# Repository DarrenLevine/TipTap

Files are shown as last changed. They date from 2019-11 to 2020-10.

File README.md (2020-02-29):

# TipTap

A 3d-printed bipedal robot. A low-cost desktop option for semi-direct drive walking research.

AssembledRobotAnimation

## Software

### Dependencies

* python >= 3.5
* pybullet
* numpy

A single python library "tiptap.py" is provided to interface to both Simulation and Hardware.
Its provides identical function calls on either target, so that you can develop your control
algorithms in simulation, and then run the idential script on hardware
without any extra work to port your code from simulation to hardware.

To get started, run, and read:
**software/example_OperatingTipTap.py**

If you're not connected to hardware a pybullet simulation will automatically start:
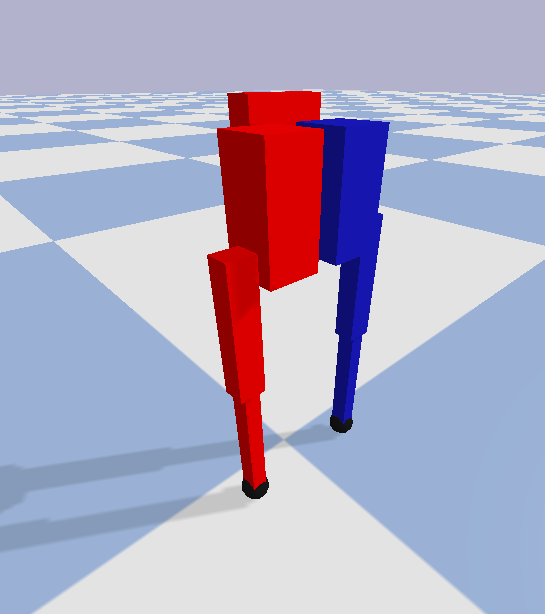
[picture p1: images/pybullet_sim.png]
pybullet_sim


If you are connected to hardware, you'll automatically be able to control the robot.

## Components

Please let me know if you find these directions difficult or find mistakes, thank you!

### Manufactured Components

* Qty 4. TipTap Motors: <https://github.com/DarrenLevine/TipTapMotor>

### Printed Components

Note: I used the parts/LulzbotMini_TipTap.curaprofile on my lulzbot mini to print all of the parts in esun PLA+.

* Qty 1. parts/BeagleBoneBlue_CaseW_RS485USB-Inner.STL
* Qty 1. parts/BeagleBoneBlue_CaseW_RS485USB-Outer.STL
* Qty 2. parts/DualMotorPCBspacer.STL
* Qty 2. parts/HipPulleyHub-Gear.STL
* Qty 2. parts/HipPulleyHub-PressurePlate.STL
* Qty 4. parts/LowerLeg.STL
* Qty 1. parts/PelvisBracket.STL
* Qty 1. parts/PelvisBracketForServos_WBuckConv.STL
* Qty 2. parts/SwivelPlate.STL
* Qty 2. parts/SwivelPlateMirror.STL
* Qty 2. parts/SwivelPlateServoMount.STL
* Qty 2. parts/SwivelPlateServoMountMirror.STL
* Qty 2. parts/UpperLegGeared-Leg.STL
* Qty 2. parts/UpperLegGeared-PressurePlate.STL
* Qty 2. parts/UpperLegHubGear.STL
* Qty 2. parts/UpperLegOuter.STL

### Purchased Components

* Qty 4. 623ZZ 3mm x 10mm x 4mm Shielded Deep Groove Precision Ball Bearing
* Qty 6. MR63ZZ L-630 673ZZ Ball Bearings
* Qty 2. AST 6706-2RS Thin Section Bearing
* Qty 2. MG92B servos
* Qty 2. BESTORQ 300-3M-6 3M Timing Belt
* Qty 1. BeagleBone Blue (BBB)
* Qty 1. LM2596 Buck Converter (set to output ~7.4v for the BBB)
* Qty 1. Mini Micro ZH 1.5 3-Pin JST Connector (to connect LM2596 to BBB)
* Qty 1. JBtek USB to RS485 Converter Adapter ch340T
* Qty 1. UCEC Short SuperSpeed USB 3.0 Extension Cable - Left/Right angle
* Qty 4. uxcell 304 Stainless Steel Dowel Pin 3mmx30mm
* Qty 2. uxcell 304 Stainless Steel Dowel Pin 3mmx10mm
* Qty 2. Rubber vacuum cap 1/4" Tube OD, 1-1/4" Long
* Qty 4. M3x8mm Nylon bolt and nut
* Qty ~200. 96817A156 Thread Forming Screw for Thin Plastic
* Qty ~6. Mini zip ties
* Qty ~. Your preference for connectors and wires, I used 7 XT30U connectors with 18AWG silicon wires for power

### Recommended Support Components

* ~24V Power: A benchtop power supply, lipos, or a 24V ~10A power adapter.
* A soldering station, some spare silicon wire, wire cutters, strippers, and snips
* A T6 torx screwdriver for the 96817A156 screws
* A phillips screwdriver for the nylon bolts
* Superglue or epoxy to fix the knee joint 3mmx30mm pins in place

## Pictures / Assembly References

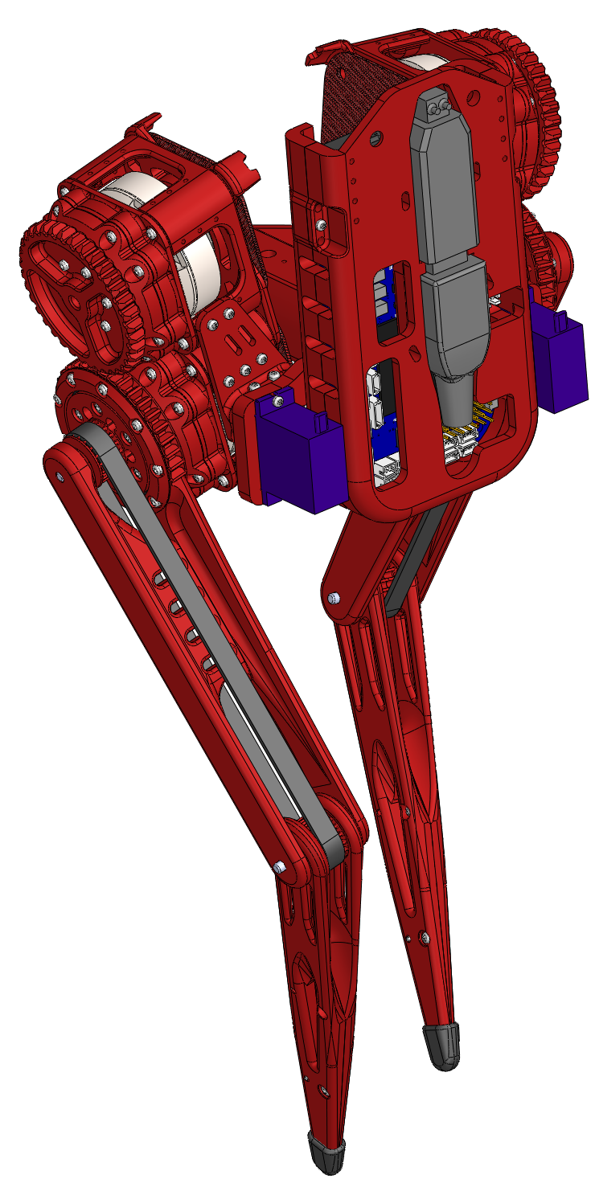
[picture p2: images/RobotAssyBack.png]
RobotAssyBack

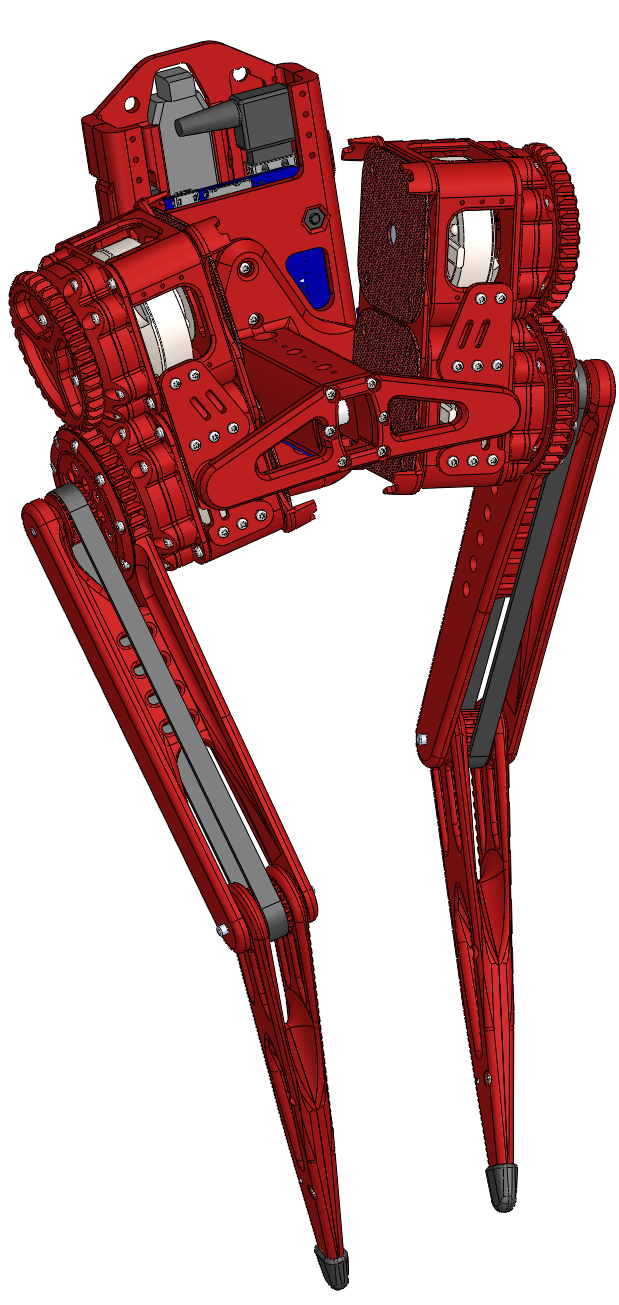
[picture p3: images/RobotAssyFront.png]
RobotAssyFront


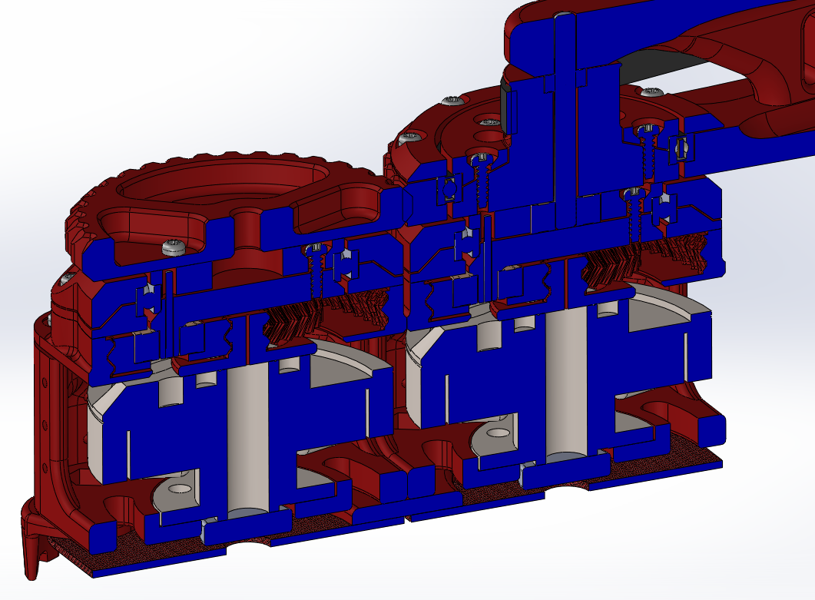
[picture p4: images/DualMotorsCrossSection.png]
DualMotorsCrossSection

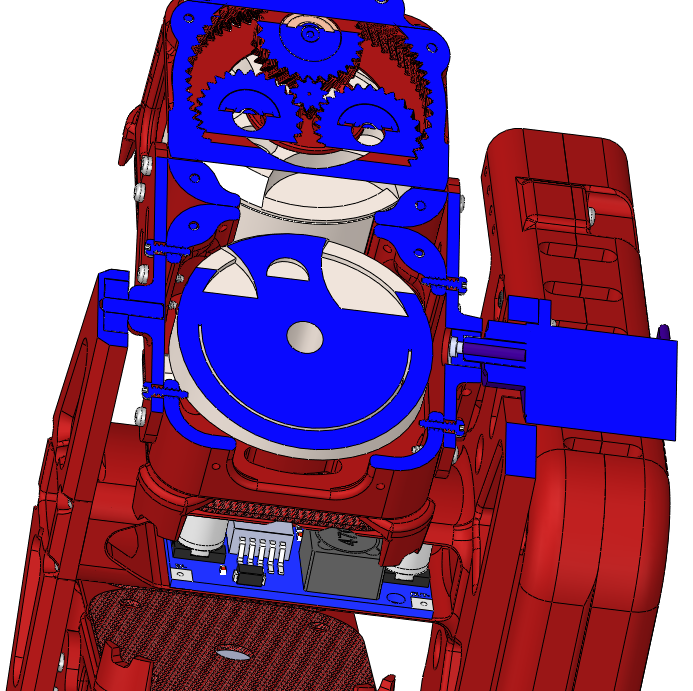
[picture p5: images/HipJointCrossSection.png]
HipJointCrossSection

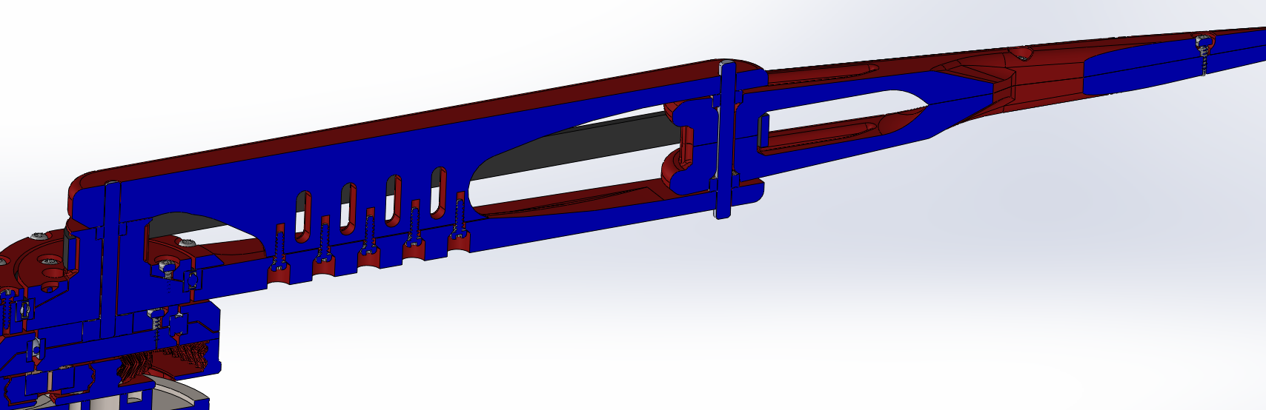
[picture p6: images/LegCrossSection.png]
LegCrossSection


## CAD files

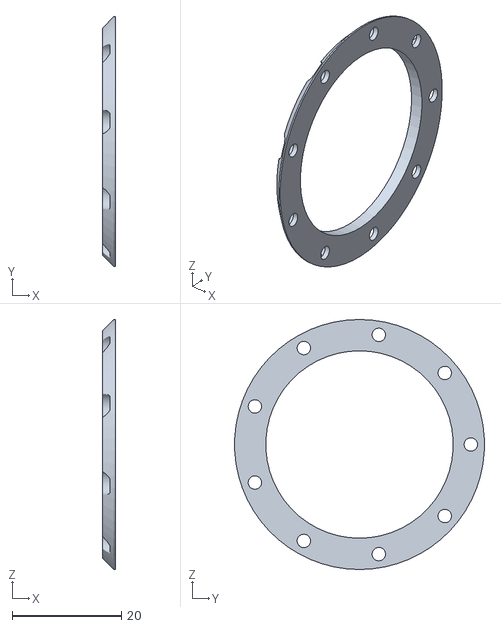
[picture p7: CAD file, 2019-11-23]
parts/UpperLegGeared-PressurePlate.STL
2.30 x 45.7 x 45.8

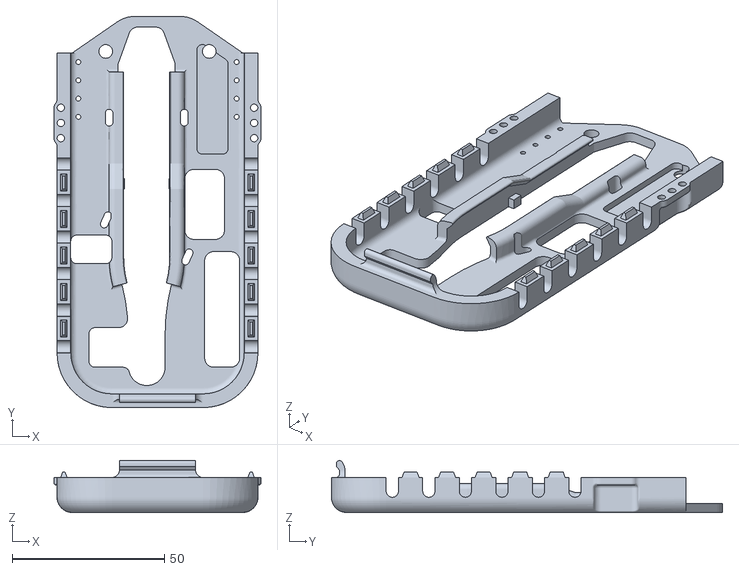
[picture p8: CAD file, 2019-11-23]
parts/BeagleBoneBlue_CaseW_RS485USB-Outer.STL
68.0 x 128.5 x 17.1

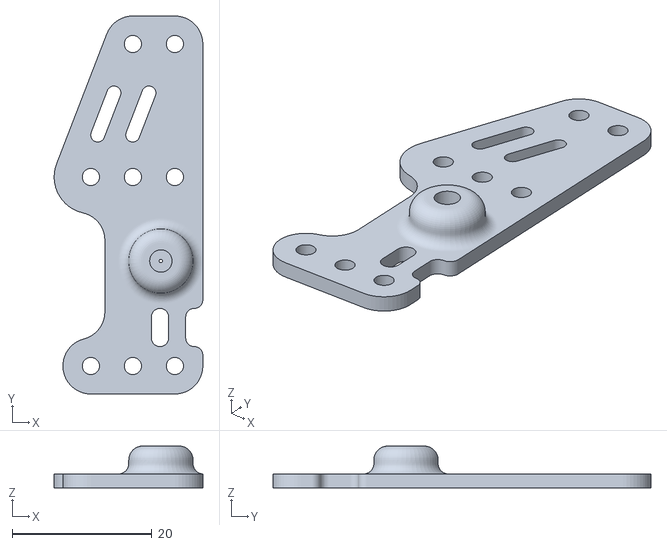
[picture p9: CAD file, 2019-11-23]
parts/SwivelPlate.STL
21.2 x 54.0 x 6.00

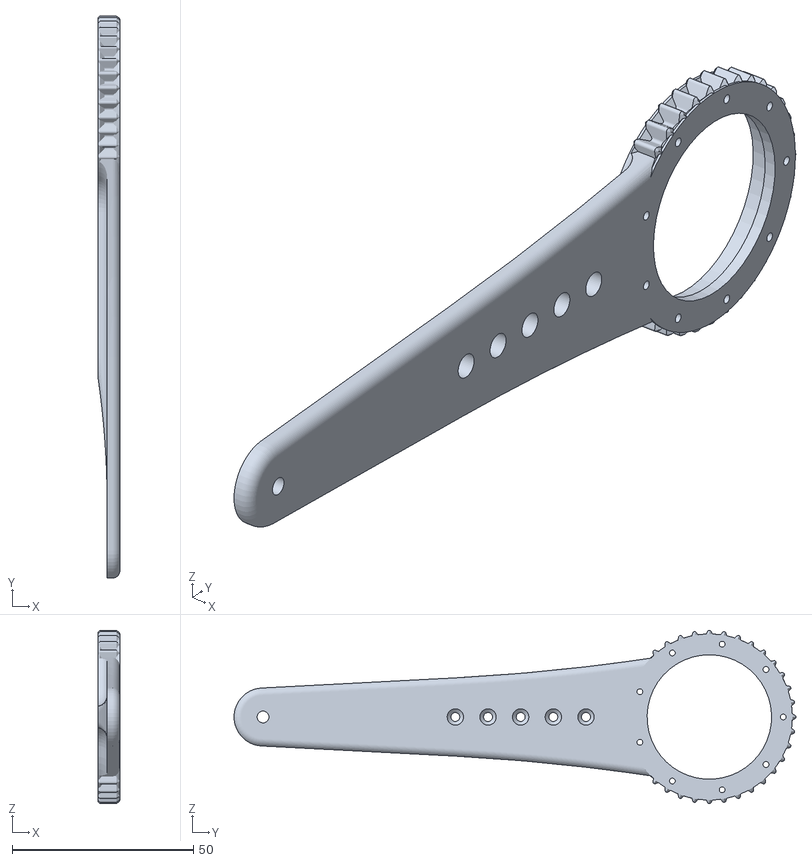
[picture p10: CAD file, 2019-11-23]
parts/UpperLegGeared-Leg.STL
6.00 x 154.9 x 47.8

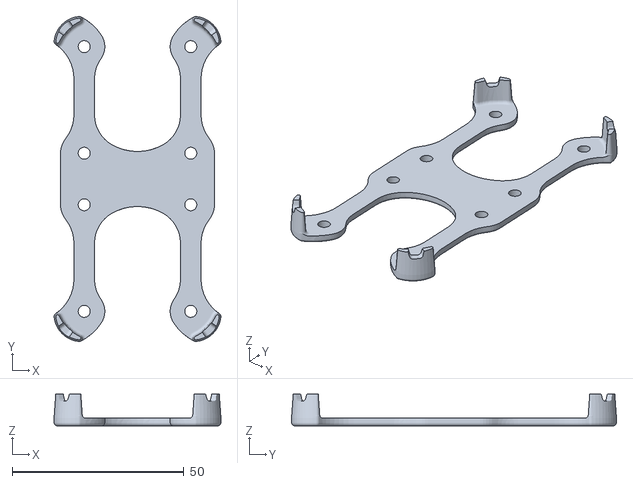
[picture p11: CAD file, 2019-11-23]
parts/DualMotorPCBspacer.STL
48.6 x 94.6 x 9.25

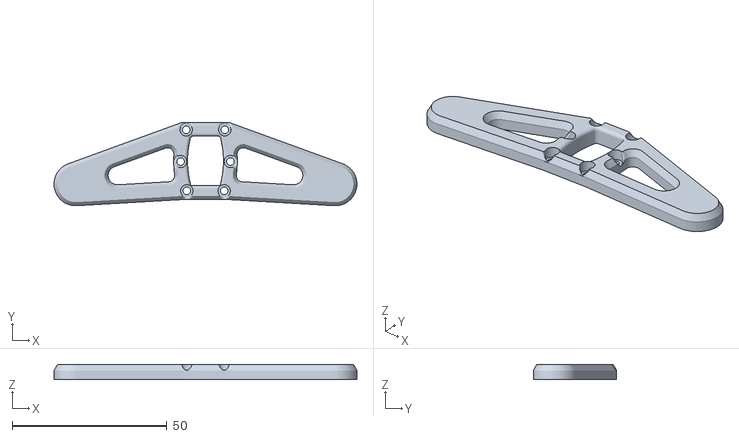
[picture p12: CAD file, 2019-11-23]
parts/PelvisBracket.STL
98.0 x 27.0 x 5.00

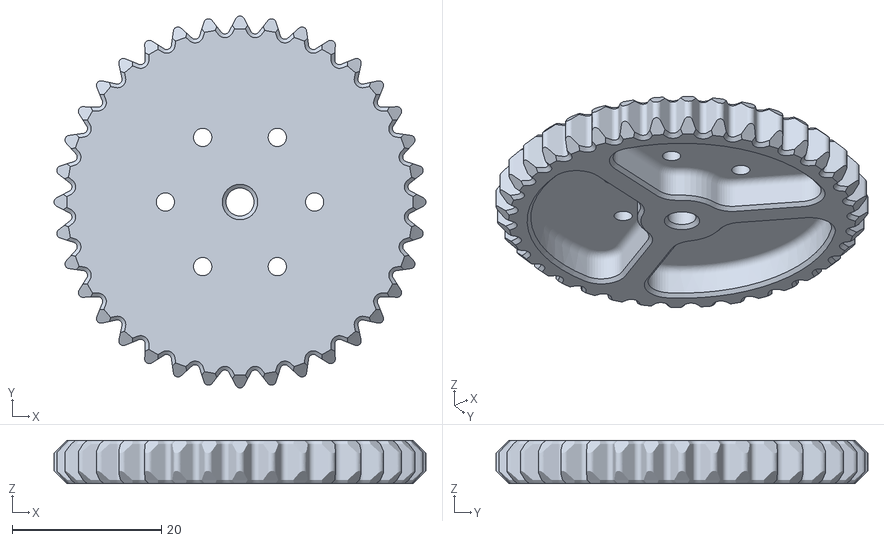
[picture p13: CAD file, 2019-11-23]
parts/UpperLegHubGear.STL
49.9 x 49.9 x 5.80

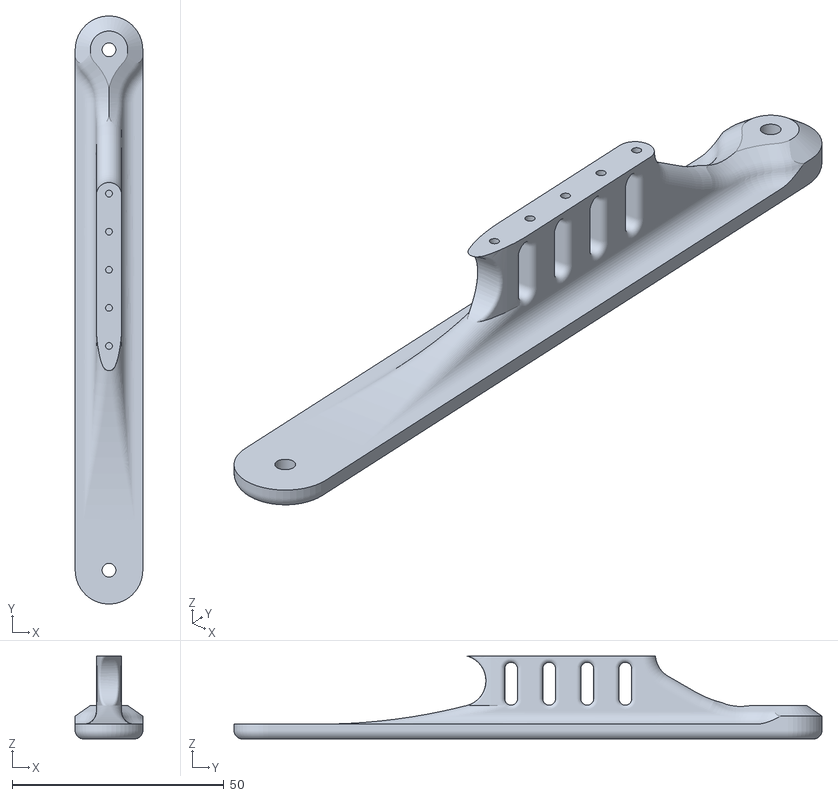
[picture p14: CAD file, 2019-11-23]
parts/UpperLegOuter.STL
16.0 x 139.0 x 19.6

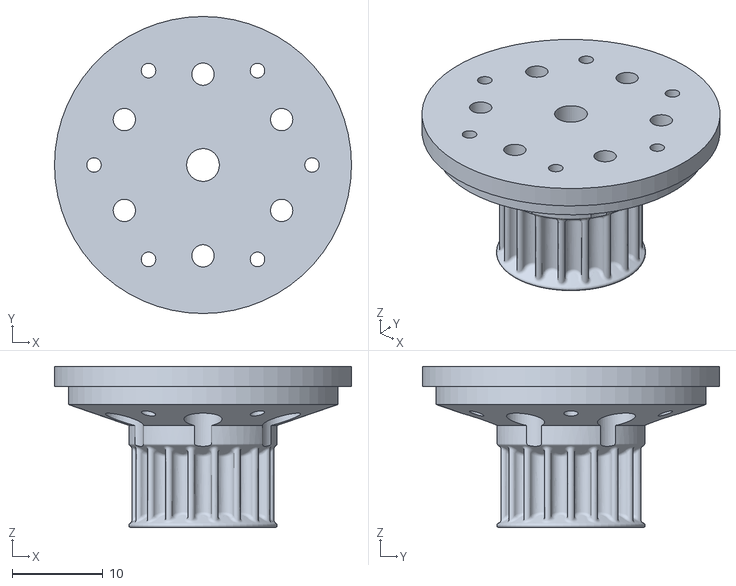
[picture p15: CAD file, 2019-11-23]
parts/HipPulleyHub-Gear.STL
32.7 x 32.7 x 17.7

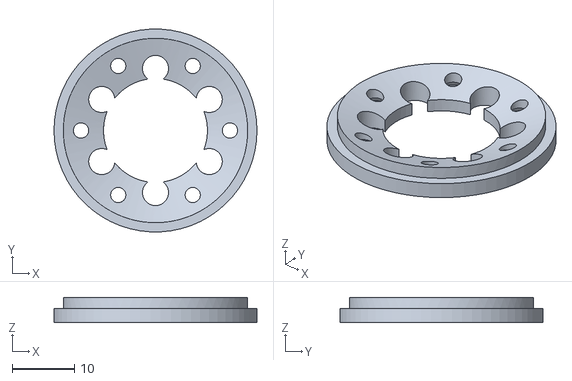
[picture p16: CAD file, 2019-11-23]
parts/HipPulleyHub-PressurePlate.STL
32.7 x 32.7 x 4.09

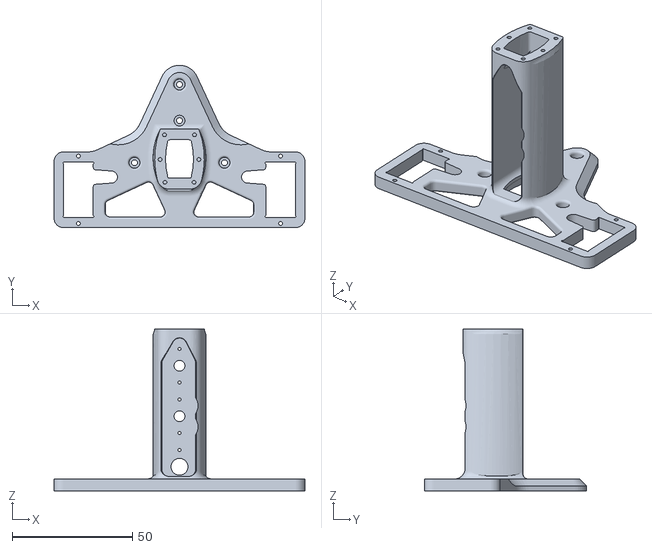
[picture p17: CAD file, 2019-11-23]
parts/PelvisBracketForServos_WBuckConv.STL
104.3 x 67.5 x 67.2

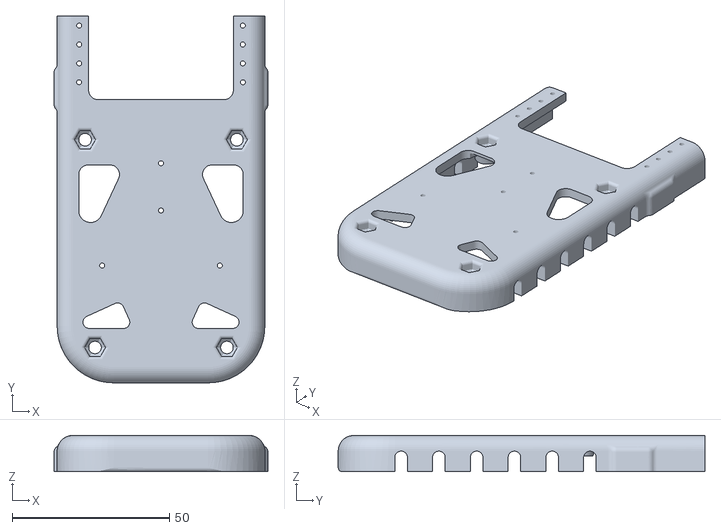
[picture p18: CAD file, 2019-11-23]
parts/BeagleBoneBlue_CaseW_RS485USB-Inner.STL
68.0 x 116.5 x 11.5

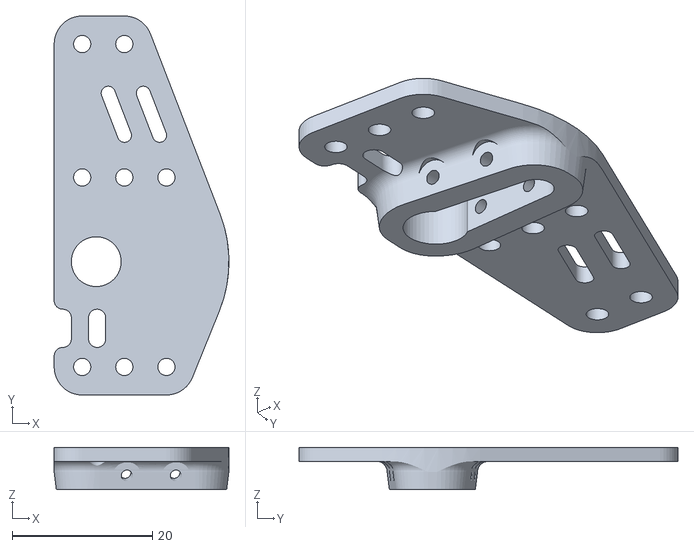
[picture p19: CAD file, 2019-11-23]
parts/SwivelPlateServoMountMirror.STL
24.9 x 54.0 x 6.00

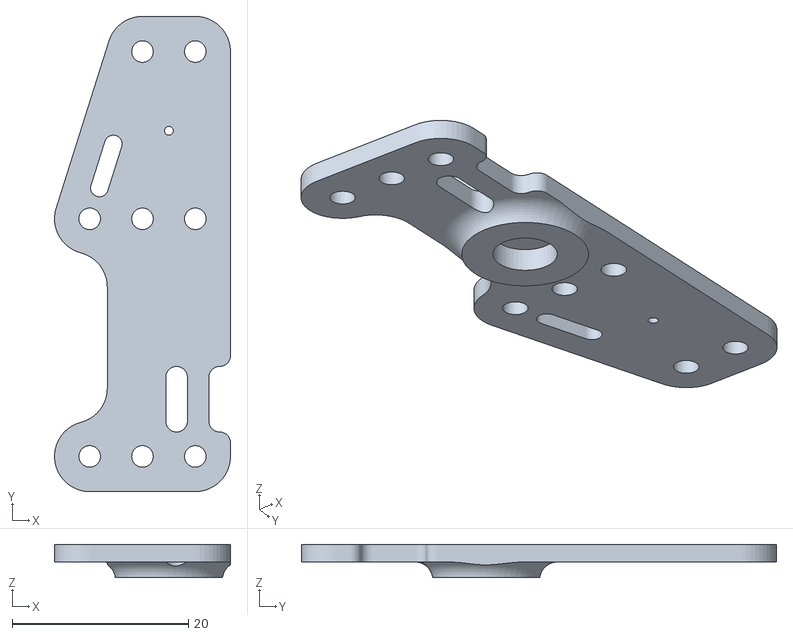
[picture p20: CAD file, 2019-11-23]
parts/SwivelPlateMirror.STL
20.0 x 54.0 x 3.75

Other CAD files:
parts/SwivelPlateServoMount.STL
parts/LowerLeg.STL

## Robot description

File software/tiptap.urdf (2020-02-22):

<?xml version="1.0" encoding="utf-8"?>
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
<robot name="tiptap" xmlns:xacro="http://www.ros.org/wiki/xacro">
  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
  <link name="torso">
    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
    <inertial>
      <origin rpy="1.57079632679 0 0" xyz="0 0 0"/>
      <mass value="0.1556"/>
      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
    </inertial>
  </link>
  <link name="hip_right">
    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
    <inertial>
      <origin rpy="0 0 0" xyz="0 0 0.047"/>
      <mass value="0.1945"/>
      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
    </inertial>
  </link>
  <link name="hip_left">
    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
    <inertial>
      <origin rpy="0 0 0" xyz="0 0 0.047"/>
      <mass value="0.1945"/>
      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
    </inertial>
  </link>
  <link name="upper_leg_right">
    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
    <inertial>
      <origin rpy="0 0 0" xyz="0 0 -0.0615"/>
      <mass value="0.05835"/>
      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
    </inertial>
  </link>
  <link name="upper_leg_left">
    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
    <inertial>
      <origin rpy="0 0 0" xyz="0 0 -0.0615"/>
      <mass value="0.05835"/>
      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
    </inertial>
  </link>
  <link name="lower_leg_right">
    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
    <inertial>
      <origin rpy="0 0 0" xyz="0 0 -0.068"/>
      <mass value="0.05835"/>
      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
    </inertial>
  </link>
  <link name="lower_leg_left">
    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
    <inertial>
      <origin rpy="0 0 0" xyz="0 0 -0.068"/>
      <mass value="0.05835"/>
      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
    </inertial>
  </link>
  <link name="right_foot">
    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
    <inertial>
      <origin rpy="0 0 0" xyz="0 0 0"/>
      <mass value="0"/>
      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
    </inertial>
  </link>
  <link name="left_foot">
    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
    <inertial>
      <origin rpy="0 0 0" xyz="0 0 0"/>
      <mass value="0"/>
      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
    </inertial>
  </link>
  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
  <joint name="RightServo" type="revolute">
    <parent link="torso"/>
    <child link="hip_right"/>
    <axis xyz="0 1 0"/>
    <origin rpy="0 0.0 0" xyz="0.0382 0.0385 -0.047"/>
    <dynamics damping="0.01" friction="0.01"/>
    <limit effort="100" lower="-0.305432619099" upper="0.343829862643" velocity="100"/>
  </joint>
  <joint name="RightHip" type="revolute">
    <parent link="hip_right"/>
    <child link="upper_leg_right"/>
    <axis xyz="1 0 0"/>
    <origin rpy="0.0 0 0" xyz="0.0365 0 0.0235"/>
    <dynamics damping="0.01" friction="0.01"/>
    <limit effort="100" lower="-2.09439510239" upper="2.09439510239" velocity="100"/>
  </joint>
  <joint name="RightKnee" type="revolute">
    <parent link="upper_leg_right"/>
    <child link="lower_leg_right"/>
    <axis xyz="1 0 0"/>
    <origin rpy="0.0 0 0" xyz="0 0 -0.123"/>
    <dynamics damping="0.01" friction="0.01"/>
    <limit effort="100" lower="-2.09439510239" upper="2.09439510239" velocity="100"/>
  </joint>
  <joint name="LeftServo" type="revolute">
    <parent link="torso"/>
    <child link="hip_left"/>
    <axis xyz="0 1 0"/>
    <origin rpy="0 0.0 0" xyz="-0.0288 0.0385 -0.047"/>
    <dynamics damping="0.01" friction="0.01"/>
    <limit effort="100" lower="-0.305432619099" upper="0.343829862643" velocity="100"/>
  </joint>
  <joint name="LeftHip" type="revolute">
    <parent link="hip_left"/>
    <child link="upper_leg_left"/>
    <axis xyz="1 0 0"/>
    <origin rpy="0.0 0 0" xyz="-0.0365 0 0.0235"/>
    <dynamics damping="0.01" friction="0.01"/>
    <limit effort="100" lower="-2.09439510239" upper="2.09439510239" velocity="100"/>
  </joint>
  <joint name="LeftKnee" type="revolute">
    <parent link="upper_leg_left"/>
    <child link="lower_leg_left"/>
    <axis xyz="1 0 0"/>
    <origin rpy="0.0 0 0" xyz="0 0 -0.123"/>
    <dynamics damping="0.01" friction="0.01"/>
    <limit effort="100" lower="-2.09439510239" upper="2.09439510239" velocity="100"/>
  </joint>
  <joint name="LeftFoot" type="fixed">
    <parent link="lower_leg_left"/>
    <child link="left_foot"/>
    <origin rpy="0 0 0" xyz="0 0 -0.136"/>
  </joint>
  <joint name="RightFoot" type="fixed">
    <parent link="lower_leg_right"/>
    <child link="right_foot"/>
    <origin rpy="0 0 0" xyz="0 0 -0.136"/>
  </joint>
</robot>

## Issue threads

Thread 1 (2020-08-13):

How is it going?

ErikOrjehag, 2020-08-13:
Did you make any progress with the control algoritm from your last Youtube video? I find this project very interesting and would like to explore something similar 🙂

DarrenLevine, 2020-10-05:
Not much progress recently, mostly due to lack of free time, and technical hurdles. The two technical issues I've been working to overcome are 1) the calculations for non-dimensionally reduced models are very expensive and so it's hard to make high rate controllers when trying to take into account the full dynamic in the math 2) the uart connection to the motors are daisy chained in a way that again limits the controller's bandwidth. So, I've been experimenting with developing a lower bandwidth controller (which can be done... here is an example of a very low rate controller that still has high performance https://github.com/DarrenLevine/rigmech/blob/master/example_ControlledPendulum.gif). An alternative would be to move to a higher rate CAN bus motor controller such as the moteus controller, and work to dimensionally reduce my model.

Closed 2020-10-05.

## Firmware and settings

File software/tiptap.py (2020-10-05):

'''
Python TipTap (tiptap.py) interface
Tested in python 3.5 and 3.7

This module:
* Detects if hardware is available
* if available, utilizes pyds.py to communicate with the hardware
* if not available, creates a pybullet simulation
* uses the same interface for both, so the same control script
  can be used for both the simulator and the hardware

See the file example_OperatingTipTap.py for an overview.

'''

import importlib
import numpy as np
import enum

# Detect if the robotics cape rcpy.py that is used
# on the beaglebone blue is available, and if it is
# assume that we're on hardware
if importlib.util.find_spec("rcpy") is not None:
    _OnHardware = True
    import rcpy  # pylint: disable=import-error
    from pyds import DirectServo
    from pyds import RegisterKillOnExit
    from pyds import KillMotors
    from pyds import EnableMotors
    from pyds import SetAdditionalKillFunction
    p = None  # allow p to still be imported in hw
else:
    _OnHardware = False
    import pybullet as p
    import pybullet_data
    import time
    import atexit
    import os


class joint(enum.Enum):
    RightServo = 0
    RightHip = 1
    RightKnee = 2
    LeftServo = 4
    LeftHip = 5
    LeftKnee = 6


enum2urdf_id = {
    joint.RightServo: 0,
    joint.RightHip: 1,
    joint.RightKnee: 2,
    joint.LeftServo: 4,
    joint.LeftHip: 5,
    joint.LeftKnee: 6
}

enum2pyds_id = {
    joint.RightServo: None,
    joint.RightHip: 0,
    joint.RightKnee: 1,
    joint.LeftServo: None,
    joint.LeftHip: 2,
    joint.LeftKnee: 3
}

PositionControlable = [joint.RightServo, joint.LeftServo]
TorqueControlable = \
    [joint.RightHip, joint.RightKnee, joint.LeftHip, joint.LeftKnee]
last_sevo_angles = [0, 0]

if _OnHardware:

    # register the atexit motor killing safety functions
    RegisterKillOnExit()

    SerialPortName = '/dev/ttyUSB0'
    Broadcast = DirectServo(Port=SerialPortName)
    RightHipJoint = DirectServo(Port=SerialPortName, ID=1)
    RightKneeJoint = DirectServo(Port=SerialPortName, ID=2)
    LeftHipJoint = DirectServo(Port=SerialPortName, ID=3)
    LeftKneeJoint = DirectServo(Port=SerialPortName, ID=4)
    AllMotors = [RightHipJoint, RightKneeJoint, LeftHipJoint, LeftKneeJoint]

    # import rcpy library, This automatically initializes the robotics cape
    try:
        rcpy.mpu9250.initialize(
            enable_dmp=True,
            dmp_sample_rate=4,
            enable_fusion=True,
            enable_magnetometer=False
        )
    except Exception:
        pass
    rcpy.set_state(rcpy.RUNNING)
    _RightLegServo = rcpy.servo.Servo(5)
    _LeftLegServo = rcpy.servo.Servo(6)
    max_t = 0.3
    clck1 = rcpy.clock.Clock(_RightLegServo, 0.05)
    clck2 = rcpy.clock.Clock(_LeftLegServo, 0.05)
    clck1.start()
    clck2.start()

    ServoRailOn = False

    def EnableServos():
        global ServoRailOn
        ServoRailOn = False

    def KillServos():
        global ServoRailOn
        rcpy.servo.disable()
        ServoRailOn = True

    def _InitServosOnce():
        global ServoRailOn
        if not ServoRailOn:
            rcpy.servo.enable()
            _RightLegServo.set(0.0)
            _LeftLegServo.set(0.0)
            ServoRailOn = True

    def RightLegServoPWM(PWM_Val):
        _InitServosOnce()
        actual_PWM_Val = min(max(PWM_Val, -max_t), max_t)
        _RightLegServo.set(actual_PWM_Val)
        return actual_PWM_Val

    def LeftLegServoPWM(PWM_Val):
        _InitServosOnce()
        actual_PWM_Val = min(max(PWM_Val, -max_t), max_t)
        _LeftLegServo.set(actual_PWM_Val)
        return actual_PWM_Val

    def range_remap(rangeinput, rangeoutput, Input):
        CorrectedInput = min(max(Input, rangeinput[0]), rangeinput[1])
        Converted = (CorrectedInput-rangeinput[0]) / \
            (rangeinput[1]-rangeinput[0]) * \
            (rangeoutput[1]-rangeoutput[0]) + \
            rangeoutput[0]
        return (Converted, CorrectedInput)

    Rservo_Cal = \
        (
            [-19.7*np.pi/180, 17.5*np.pi/180],
            [0.45*np.pi/180, -0.26*np.pi/180]
        )

    def RightLegServo(AngleOutwardRad):
        global last_sevo_angles
        PWM_val, ActualAngle = range_remap(
            Rservo_Cal[0],
            Rservo_Cal[1], AngleOutwardRad)
        _InitServosOnce()
        _RightLegServo.set(PWM_val)
        last_sevo_angles[1] = ActualAngle
        return ActualAngle

    Lservo_Cal = \
        (
            [-19.7*np.pi/180, 17.5*np.pi/180],
            [-0.35*np.pi/180, 0.39*np.pi/180]
        )

    def LeftLegServo(AngleOutwardRad):
        global last_sevo_angles
        PWM_val, ActualAngle = range_remap(
            Lservo_Cal[0],
            Lservo_Cal[1], AngleOutwardRad)
        _InitServosOnce()
        _LeftLegServo.set(PWM_val)
        last_sevo_angles[0] = ActualAngle
        return ActualAngle

    def RightLegServoDeg(AngleOutwardDeg):
        return RightLegServo(AngleOutwardDeg*np.pi/180)

    def LeftLegServoDeg(AngleOutwardDeg):
        return LeftLegServo(AngleOutwardDeg*np.pi/180)

    def GetIMUData():
        rcpy.mpu9250.read_accel_data()
        data = rcpy.mpu9250.read()
        return {**{"pitch": data['tb'][0],
                   "roll": data['tb'][1],
                   "yaw": data['tb'][2]}, **data}

    def GetIMUDataDeg():
        rcpy.mpu9250.read_accel_data()
        data = rcpy.mpu9250.read()
        result = {}
        result["pitch"] = data['tb'][0]*180./np.pi-90.
        result["roll"] = data['tb'][1]*180./np.pi
        result["yaw"] = data['tb'][2]*180./np.pi
        result["accel"] = data['accel']
        return result

    RobotEnabled = True

    def EnableIf_OtherwiseDisable(Condition):
        ''' Enables or kills the robot based on the
        passed boolean'''
        global RobotEnabled
        if Condition:
            if not RobotEnabled:
                EnableServos()
                EnableMotors()
                RobotEnabled = True
        elif RobotEnabled:
            KillServos()
            KillMotors(AllMotors)
            RobotEnabled = False

    def ExitProgram():
        print("Exiting!")
        KillServos()
        KillMotors(AllMotors)
        rcpy.exit()

    # Set ExitProgram to also run at exit()
    # which makes sure the robot cape (rcpy)
    # is killed safely
    SetAdditionalKillFunction(ExitProgram)

    dt_actual = 1. / 240.
    last_time = time.time()
    start_time = time.time()

    class TipTap():

        RightServo_num = 0
        RightHip_num = 1
        RightKnee_num = 2
        LeftServo_num = 3
        LeftHip_num = 4
        LeftKnee_num = 5

        @staticmethod
        def OnHardware():
            return True
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

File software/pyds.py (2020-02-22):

'''
Python DirectServo (pyds.py) interface
Tested in python 3.5 and 3.7

'''
import serial
import atexit
import time

GlobalKillSwitch = False

# Static lifetime RS485 connections are stored in PortMap, which
# allows many DirectServo class instances to be bound to ports
# without clashing port connections
PortMap = {}

# the following would be better organized as class static member
# variables/methods, but it's more performant to avoid dot lookups
# in this manner


def Decimal2HexStr(x):
    return hex(abs(x))[2:].zfill(2).upper()[-2:]


d2hi = {x: int.from_bytes(Decimal2HexStr(x).encode('utf-8'), 'big')
        for x in range(256)}
BroadcastID = 0xFF
BROADCAST = d2hi[BroadcastID]
# passes torque parameter: [-255 to 255]
CMD_TORQUE = int.from_bytes(b"T", 'big') << 32
# passes ID parameter: [0 to 255] 0xFF is reserved for broadcast
CMD_SETID = int.from_bytes(b"I", 'big') << 24
CMD_CALIBRATE = int.from_bytes(b"C", 'big') << 8  # no passed parameters
CMD_GETANGLE = int.from_bytes(b"a", 'big') << 8  # no passed parameters
CMD_ZEROANGLE = int.from_bytes(b"Z", 'big') << 8  # no passed parameters
# CMD_FAILSAFE passes:{
# +/-;
# uint8_t FailoverTorqueRatio;
# uint8_t SearchingTorqueRatio;
# uint8_t FailAtLimitOffsetDeg_MSByte;
# uint8_t FailAtLimitOffsetDeg_LSByte;}
CMD_FAILSAFE = int.from_bytes(b"F", 'big') << 24
# no passed parameters (resets flash)
CMD_RESET = int.from_bytes(b"R", 'big') << 8
NEWLINE_BYTE = int.from_bytes(b'\n', 'big')
PLUS_SYM_BYTE = int.from_bytes(b'+', 'big') << 16
MINUS_SYM_BYTE = int.from_bytes(b'-', 'big') << 16


def RatioToByte(x):
    return (MINUS_SYM_BYTE if x < 0 else PLUS_SYM_BYTE,
            int((1 if x > 1 or x < -1 else abs(x))*0xFF))


def Torque_BYTES(Dest, TorqueRatio):
    tr_prefix, TorqueRatio = RatioToByte(TorqueRatio)
    return ((d2hi.get(Dest, BROADCAST) << 40) | CMD_TORQUE |
            ((tr_prefix | d2hi.get(TorqueRatio, 0xFF)) << 8) |
            NEWLINE_BYTE).to_bytes(7, 'big')


def SetID_BYTES(Dest, NewID):
    if NewID > 0xFF:
        raise ValueError("NewID cannot be larger than 0xFF")
    return ((d2hi.get(Dest, BROADCAST) << 32) |
            CMD_SETID | (d2hi[NewID] << 8) |
            NEWLINE_BYTE).to_bytes(6, 'big')


def Calibrate_BYTES(Dest):
    return ((d2hi.get(Dest, BROADCAST) << 16) |
            CMD_CALIBRATE |
            NEWLINE_BYTE).to_bytes(4, 'big')


def GetState_BYTES(Dest):
    return ((d2hi.get(Dest, BROADCAST) << 16) |
            CMD_GETANGLE |
            NEWLINE_BYTE).to_bytes(4, 'big')


def SetZeroAngle_BYTES(Dest):
    return ((d2hi.get(Dest, BROADCAST) << 16) |
            CMD_ZEROANGLE |
            NEWLINE_BYTE).to_bytes(4, 'big')

# FailoverTorqueRatio, torque ratio [-1.0 to 1.0]
# SearchingTorqueRatio, torque ratio search magnitude [0.0 to 1.0]
# FailAtLimitOffsetDeg, offset in degrees to failsafe [0.0 to 360.0]


def Failsafe_BYTES(Dest,
                   FailoverTorqueRatio,
                   SearchingTorqueRatio,
                   FailAtLimitOffsetDeg):
    FailAtLimitOffsetDeg = 0 if FailAtLimitOffsetDeg < 0 else int(
        FailAtLimitOffsetDeg/360.0*0xFFFF)
    if FailAtLimitOffsetDeg > 0xFFFF:
        raise ValueError("Offset cannot be larger than 360 degrees")
    tFVprefix, FailoverTorqueRatio = RatioToByte(FailoverTorqueRatio)
    if SearchingTorqueRatio < 0:
        SearchingTorqueRatio = 0
    elif SearchingTorqueRatio > 1:
        SearchingTorqueRatio = 0xFF
    else:
        SearchingTorqueRatio = int(SearchingTorqueRatio*0xFF)
    return ((d2hi.get(Dest, BROADCAST) << 32) | CMD_FAILSAFE
            | (tFVprefix | d2hi[FailoverTorqueRatio])).to_bytes(6, 'big') + \
        ((d2hi[SearchingTorqueRatio] << 40)
         | (d2hi[FailAtLimitOffsetDeg >> 8] << 24)
         | (d2hi[FailAtLimitOffsetDeg & 0xFF] << 8)
         | NEWLINE_BYTE).to_bytes(7, 'big')


def Reset_BYTES(Dest):
    return ((d2hi.get(Dest, BROADCAST) << 16) |
            CMD_RESET |
            NEWLINE_BYTE).to_bytes(4, 'big')


class DirectServo():
    """A helper class for controlling the DirectServo, it is not built for
    efficiency, (use C/C++ if you need that) but instead from a desire
    to mess around with the controller easily via a python interface.

    Examples:

        YourServo = DirectServo(ID = 23) # initialize a communication object
                                         # to ID 23
        YourServo.SetID()                # send a broadcast signal to
                                         # set ID = 23
        YourServo.Calibrate()            # calibrate servo with ID = 23
        Angle = YourServo.GetAngle()     # get the angle in degrees
        Angle = YourServo.Torque(0.25)   # set torque to 25% and return the
                                         # angle
        Angle = YourServo.SetZeroAngle() # set the angle tracked by the motor
                                         # driver to zero at its current
                                         # position
        Angle = YourServo.SetFailsafe()  # turns on a failsafe feature, and
                                         # passes optional settings:
                                         # 'failsafe':-1.0 to 1.0,
                                         # 'search':0.0 to 1.0,
                                         # 'offset': value in degrees from
                                         # searched limit to set failsafe
                                         # at [0 to 360]
        Angle = YourServo.Reset()        # resets the board and clears the
                                         # flash memory to default settings
    """

    def __init__(self,
                 ID=BroadcastID,
                 Port=None,
                 BaudRate=115200,
                 Timeout=0.5):
        if Port is None:
            raise RuntimeError(
                "Must specify a serial port when creating a" +
                " DirectServo object. Example: DirectServo(Port = 'COM1')"
            )
        self.ID = ID
        self.RS485 = PortMap.get(Port)
        if self.RS485 is None:
            self.RS485 = serial.Serial(
                port=Port, baudrate=BaudRate, timeout=Timeout)
            PortMap[Port] = self.RS485
            if self.RS485.isOpen():
                self.RS485.flushInput()
                self.RS485.flushOutput()
        if not self.RS485.isOpen():
            raise RuntimeError(
                "{}.RS485({}) connection not open".format(self, self.ID))
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

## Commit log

2019-11-23 added parts
    [BeagleBoneBlue_CaseW_RS485USB-Inner.STL, BeagleBoneBlue_CaseW_RS485USB-Outer.STL, DualMotorPCBspacer.STL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]
2020-02-22 added software
    [BeagleBoneBlue_CaseW_RS485USB-Inner.STL, BeagleBoneBlue_CaseW_RS485USB-Outer.STL, DualMotorPCBspacer.STL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]
2020-02-22 moved stl files into parts folder
    [BeagleBoneBlue_CaseW_RS485USB-Inner.STL, BeagleBoneBlue_CaseW_RS485USB-Outer.STL, DualMotorPCBspacer.STL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]
2020-10-05 improved simulation stability by exposing fixedTimeStep in GetTimeStep()
    [example_OperatingTipTap.py, tiptap.py]
